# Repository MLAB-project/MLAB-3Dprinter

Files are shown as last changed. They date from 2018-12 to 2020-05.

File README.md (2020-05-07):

RebeliX
=======
RebeliX – a 3D printer inspired by constructions of Rebel II a Prusa i3. Licensed as GPLv3. Howto and list of materials is available on www.RebeliX.cz (currently only in Czech, we are working on it, help is appreciated).

Features
=====

* Piezoelectric based precise Z-calibration
* Symmetric motor configuration push-pull to minimize belt stretching in printing of corners

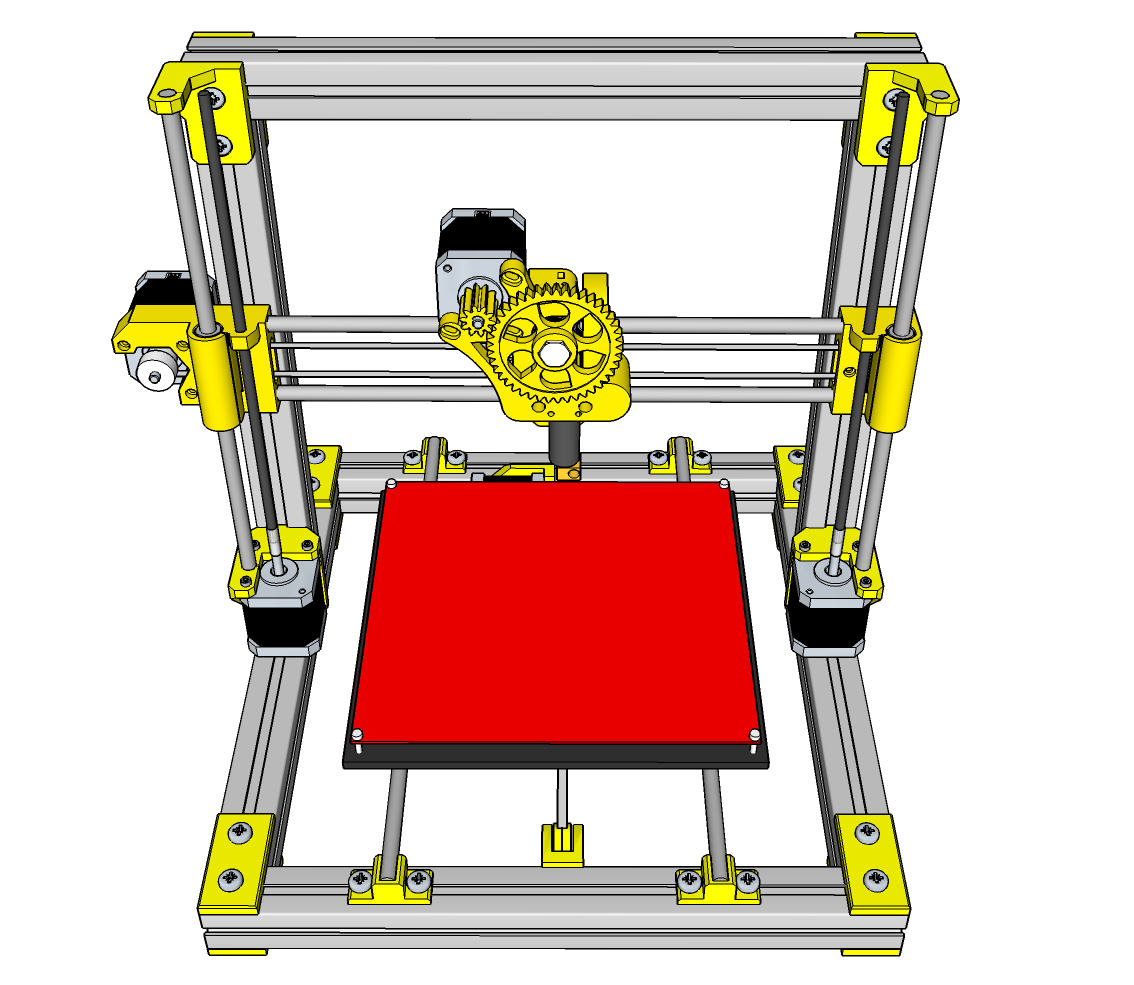
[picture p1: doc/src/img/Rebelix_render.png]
RebeliX Preview of assembled printer


Build
=====

   sudo pip install stlsort

To continue OpenSCAD has to be installed and available as `openscad` command.

1. Make necessary changes to configuration.scad according to printer that prints the parts and available hardware. 
* Generate a calibration object by `make calibration`.
* Print generated calibration.stl and repeat the steps if unhappy.

When satisfied, run `make clean && make all`. That produces STLs with your tweeks.

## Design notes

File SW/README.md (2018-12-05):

Configuration for Rebelix after editing for MLAB

Configuration.h used to generate printer firmware by configurator available from there:
https://www.repetier.com/firmware/v092/index.php

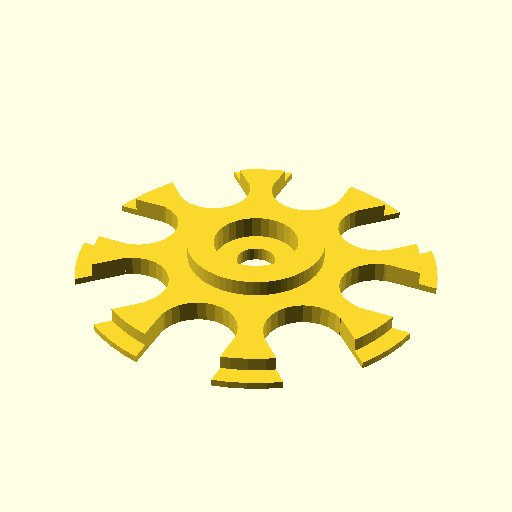
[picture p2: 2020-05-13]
doc/src/img/spool-center.png

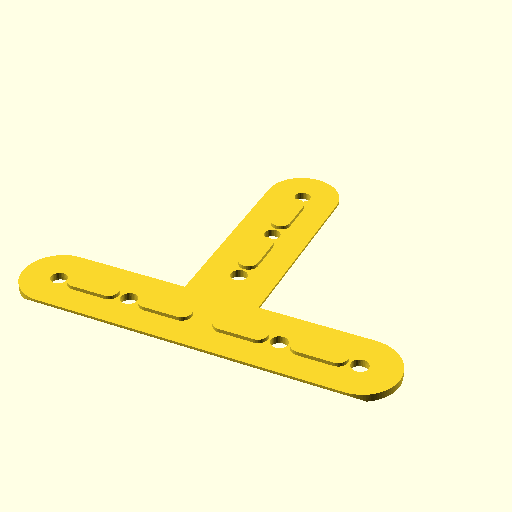
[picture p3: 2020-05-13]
doc/src/img/z-coupler.png

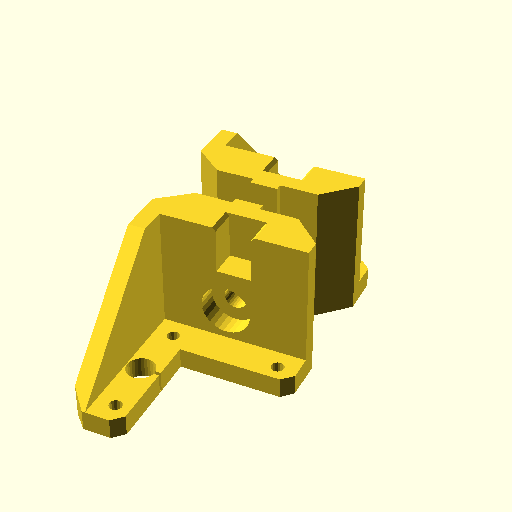
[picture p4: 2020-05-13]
doc/src/img/z-bottom.png

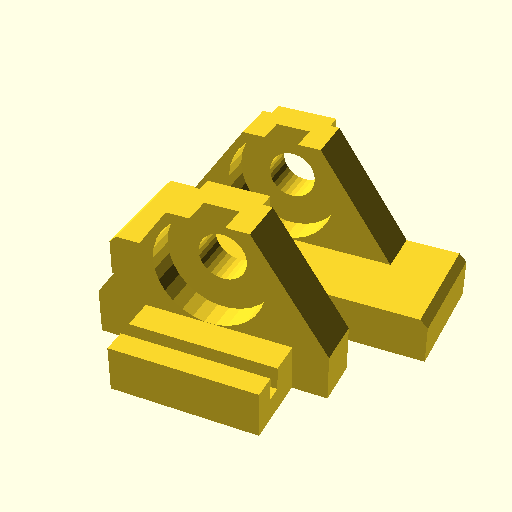
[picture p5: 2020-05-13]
doc/src/img/RAMPS_mini.png

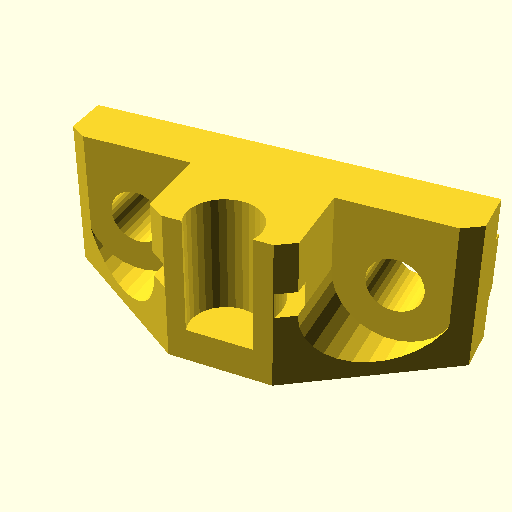
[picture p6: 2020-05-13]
doc/src/img/y-rod-holder.png

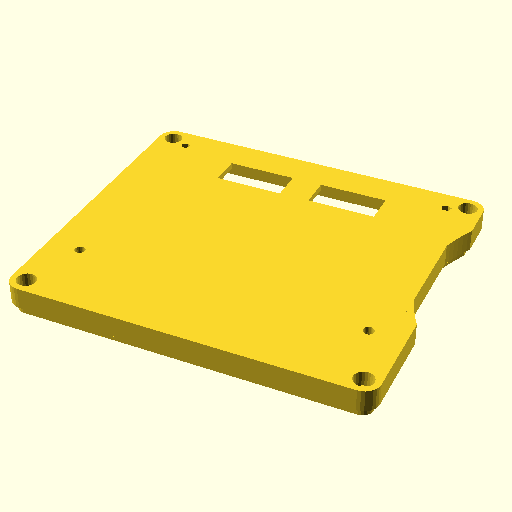
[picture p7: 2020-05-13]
doc/src/img/mods_for_display_case_back.png

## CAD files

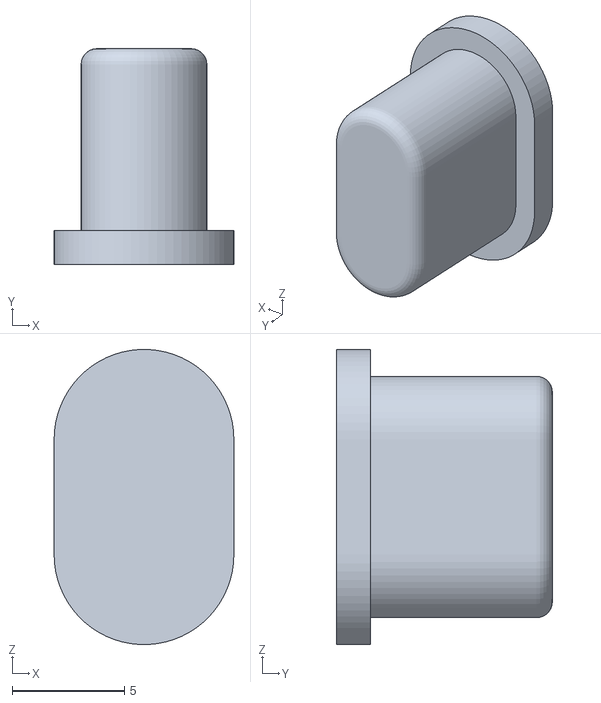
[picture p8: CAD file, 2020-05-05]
hw/cad/src/include/Case_for_the_Full_Graphic_Smart_LCD_Controllerf-Kill_Button_FGD.stl
8.00 x 9.60 x 13.1

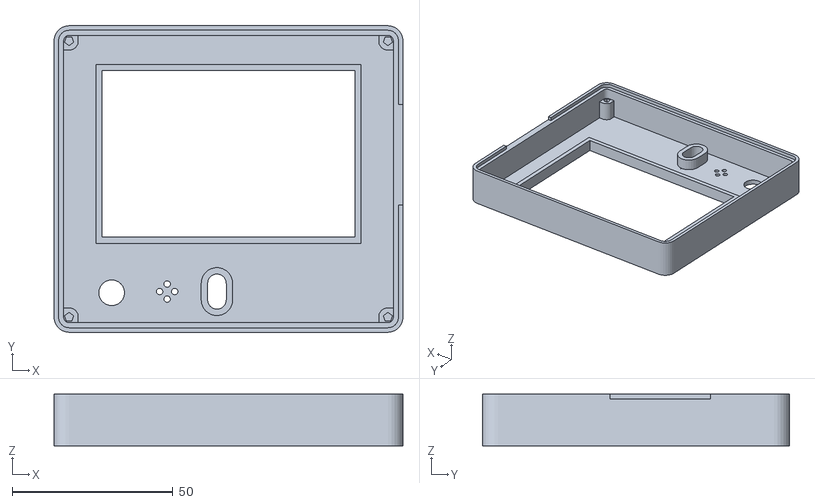
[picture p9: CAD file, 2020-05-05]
hw/cad/src/include/Case_for_the_Full_Graphic_Smart_LCD-Top_Case_FGD.stl
108.6 x 95.4 x 16.1

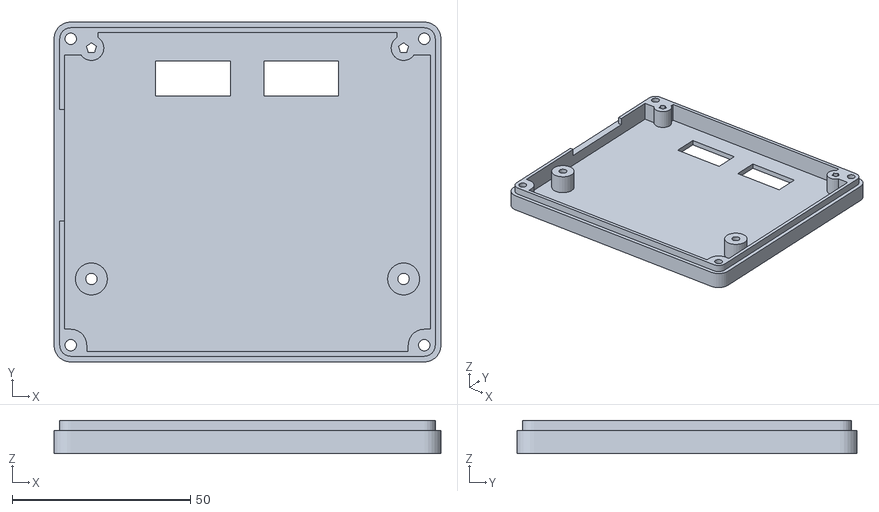
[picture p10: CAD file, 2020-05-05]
hw/cad/src/include/Case_for_the_Full_Graphic_Smart_LCD_Controller-Bottom_Case_FGD.stl
108.6 x 95.4 x 9.30

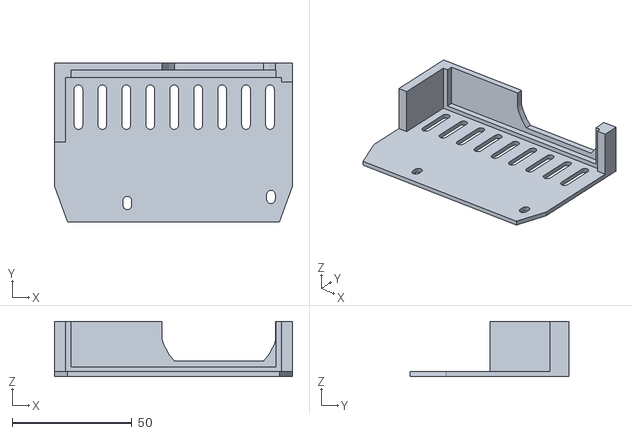
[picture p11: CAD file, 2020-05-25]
doc/src/stl/Rear_EURO_12V_240W.stl
99.4 x 66.5 x 23.0

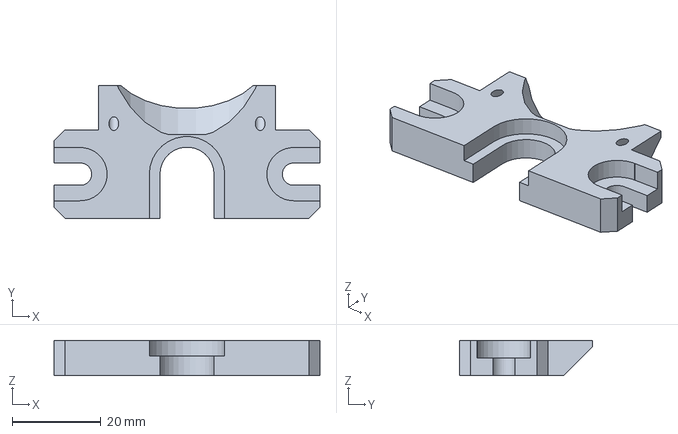
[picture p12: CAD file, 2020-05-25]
hw/amf/j-head-mount.amf
60.0 x 30.0 x 8.00 mm

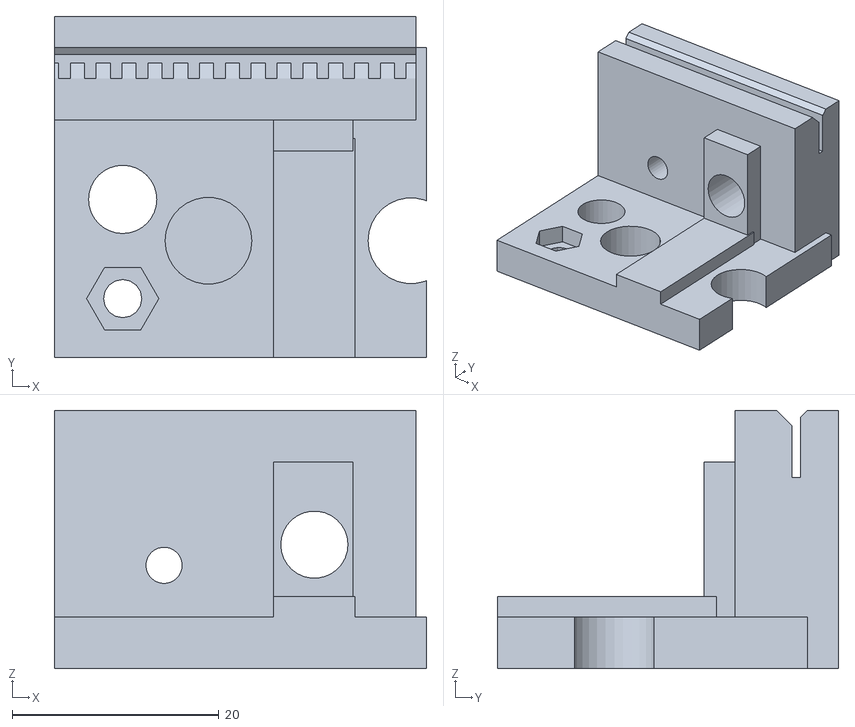
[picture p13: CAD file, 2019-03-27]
hw/cad/calibration.stl
36.0 x 33.0 x 25.0

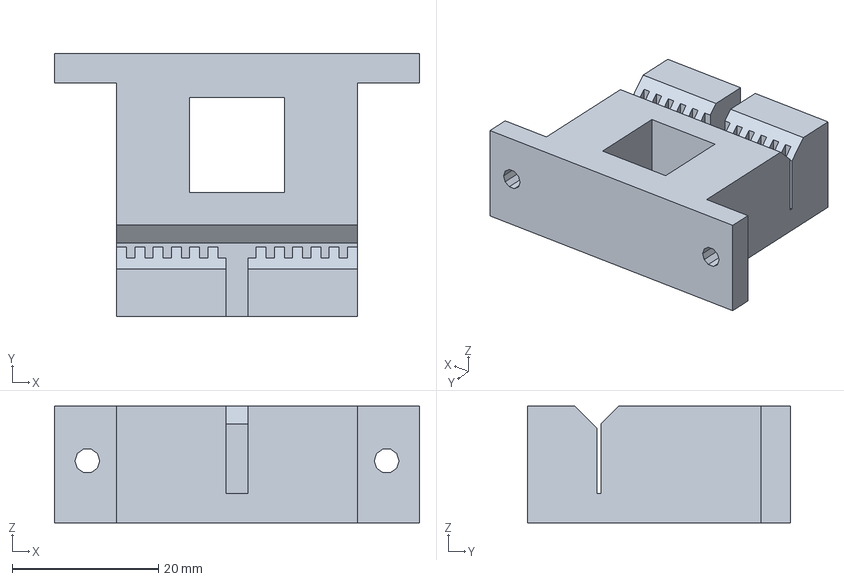
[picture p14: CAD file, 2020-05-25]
hw/amf/y-belt-holder.amf
50.0 x 36.0 x 16.0 mm

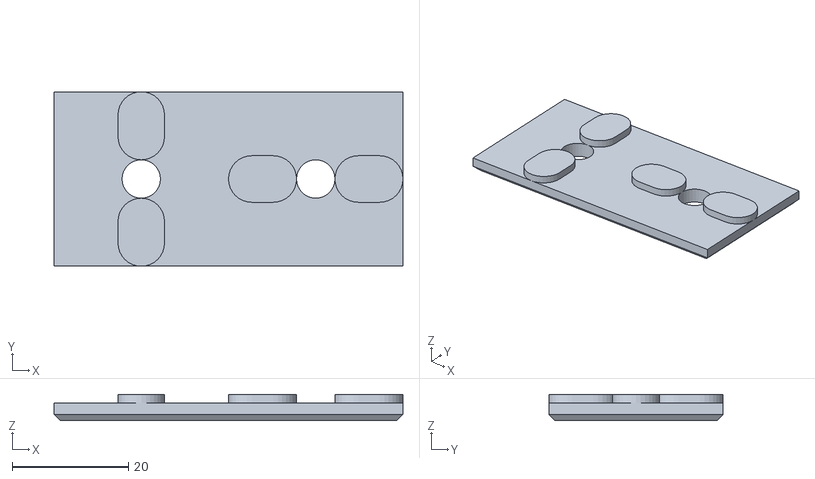
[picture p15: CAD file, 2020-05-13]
doc/src/stl/corner-coupler.stl
60.0 x 30.0 x 4.50

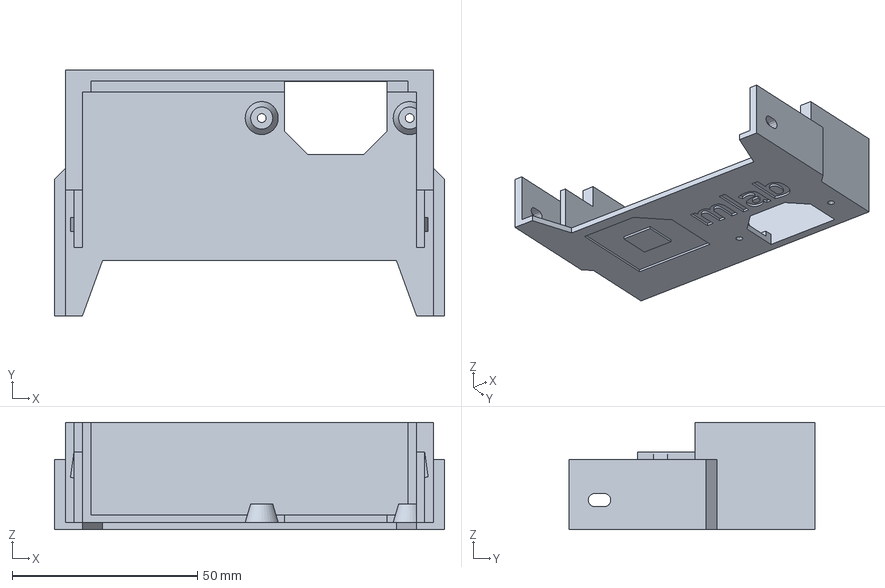
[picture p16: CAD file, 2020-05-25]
hw/amf/Front_EURO_12V_240W.amf
105.4 x 66.5 x 29.0 mm

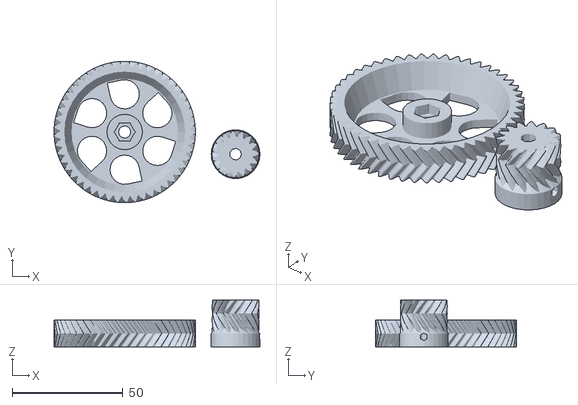
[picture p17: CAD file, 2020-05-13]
doc/src/stl/wade-gears.stl
92.9 x 63.7 x 21.0

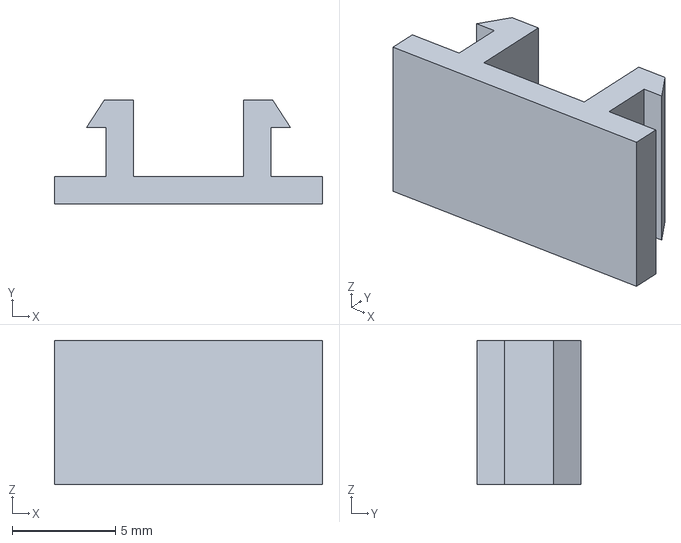
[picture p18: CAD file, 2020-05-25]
hw/amf/cable-holder.amf
13.0 x 5.04 x 7.00 mm

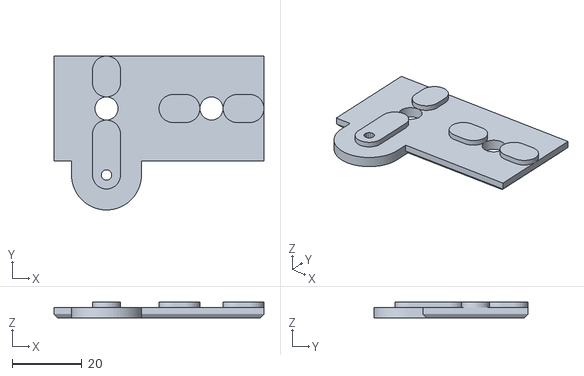
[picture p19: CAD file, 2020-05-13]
doc/src/stl/corner-coupler-bottom.stl
60.0 x 44.0 x 4.50

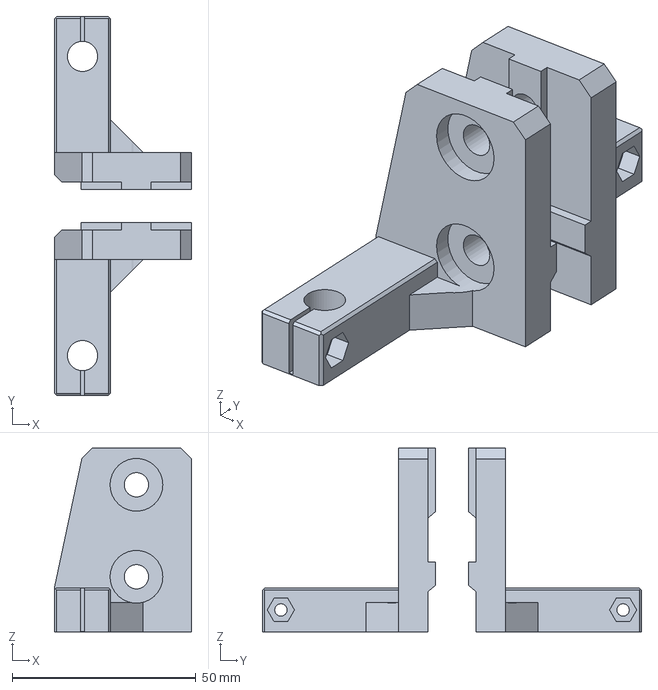
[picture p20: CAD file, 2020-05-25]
hw/amf/z-top.amf
37.3 x 103.0 x 50.0 mm

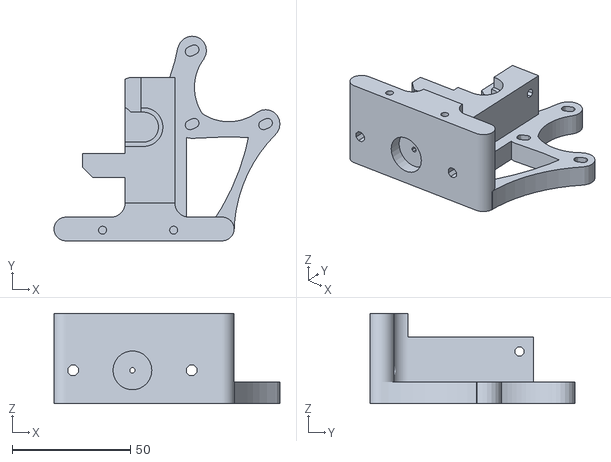
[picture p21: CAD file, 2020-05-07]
doc/src/stl/gregs-wade-625.stl
95.4 x 86.4 x 38.0

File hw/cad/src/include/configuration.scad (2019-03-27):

// Layer high for the printing [mm]
layer_height = 0.20; //Slic3r->Print Settings->Layers and perimeters->Layer height

// Spare for the screws heads [mm]
spare = 0.75;
// M6 screw diameter [mm]
M6_head_diameter = 13.6+spare;
//M6_head_diameter = 10.6+spare;
//M6_head_diameter = 12+spare;

// M6 head high (for hiding it) [mm]
//M6_head_height = 4;
M6_head_height = 3.6;
//M6_head_height = 4.5;

// Screws and rods diameters
M8_smooth_rod_diameter = 8.3;
M8_smooth_rod_diameter_catch = 8.4;
// Prumer 8mm tyce
rod_8mm_d = 8.2; //pro dil z-top
M6_diameter = 6.6;
M6_dia=M6_diameter; //pro dil z-top
M6_diamater_horizontal = 6.5;
M3_diameter = 3.7;
M3_diameter_horizontal = 3.5;

//matice trapézové tyče
TRAP_diameter_externa=22; //průmer vnější 


// Nuts diameters
M3_nut_diameter = 7.0;
M3_nut_diameter_horizontal = 6.7;

// ALU profile parameters
ALU_cut_width = 7.9;
ALU_cut_width_horizontal = 7.7;

// Sirka matky do profilu (pokud neni pouzita, tak 0)
//profile_nut_width = 9.5;
profile_nut_width = 0; //pro z-top

// Motors length/depth (for axes Z and Y)
//SX17-1003LQFE (recommended for the Z axis)
motor_length = 29.5;
//SX17-1003 (recommended for the Z axis)
//motor_length = 34;
//SX17-1005
//motor_length = 40;
//SX17-0905 - this motor is too high - the Z end stop holder has to be adjusted
//motor_length = 48;

// Extrusion width [mm]
extrusion_width = 0.66; //Slic3r->Print Settings->Advanced->Default extrusion width

/// Belt type ******************************************************

// GT2 
/*belt_tooth_distance = 2;
belt_tooth_ratio = 0.5;
belt_tooth_height = 1.4;
belt_thickness = 2.3;
*/

// T2.5
belt_tooth_distance = 2.5;
belt_tooth_ratio = 0.45;


// Tloustka rohovych spojek
// 5 mm => sroub M6x14 s podlozkou
// 3 mm => sroub M6x12 s podlozkou
coupler_thickness = 3;

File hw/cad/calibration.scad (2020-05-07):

include <./src/include/configuration.scad>

difference(){
	union(){
		cube([36,30,5]);
		translate([0,23,0])cube([35,10,25]);
		translate([M6_diameter*2+8,20,0])cube([ALU_cut_width_horizontal,11,20]);
	}
	translate([M6_diameter,M6_diameter+M3_diameter+5,-1])cylinder(r=M6_diameter/2,h=7,$fn=32);
	translate([M6_diameter,M3_diameter+2,-1]){
		cylinder(r=M3_diameter/2,h=7,$fn=16);	
		translate([0,0,3.5])cylinder(r=M3_nut_diameter/2,h=2.6,$fn=6);
	}
	translate([M6_diameter+M8_smooth_rod_diameter,M8_smooth_rod_diameter+3,layer_height])cylinder(h=7,r=M8_smooth_rod_diameter_catch/2,$fn = 30);
	translate([34.5,M8_smooth_rod_diameter+3,-1])cylinder(h=7,r=M8_smooth_rod_diameter/2,$fn = 30);
	
	translate([M6_diameter+4,34,10]) 
	rotate([90,0,0]){
		cylinder(h = 15, r=M3_diameter_horizontal/2, $fn=30);
		cylinder(h = 4, r=M3_nut_diameter_horizontal/2, $fn=6);
	}

	translate([M6_diameter*2+8+ALU_cut_width/2,34,12]) 
	rotate([90,0,0]){
		cylinder(r = M6_diamater_horizontal/2, h = 15, $fn = 30);
		cylinder(r = M6_head_diameter/2, h = 4, $fn = 30);
	}
	
	translate([-1,27,18.5])belt_holder_beltcut();
}

translate([M6_diameter*2+8,0,0])cube([ALU_cut_width,M6_diameter*2+8,7]);

module belt_holder_beltcut(){
 echo(belt_tooth_ratio*belt_tooth_distance);
 position_tweak=-1.1;
 // Belt slit
 //translate([-66,-0.5+10,3]) 
 translate([0,1.5,0])
 cube([67,0.8,15]);
 // Smooth insert cutout
 //translate([-66,-0.5+10,12]) 
 translate([0,1.5,5])
 rotate([45,0,0]) cube([67,15,15]);
 // Individual teeth
 for ( i = [0 : 23] ){
 	translate([0+i*belt_tooth_distance+position_tweak,0,0]) cube([belt_tooth_ratio*belt_tooth_distance,1.7,15]);
 }
}

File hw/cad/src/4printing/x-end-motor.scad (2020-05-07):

// PRUSA iteration3
// x end motor
// GNU GPL v3
// Josef Průša <iam@josefprusa.cz> and contributors
// http://www.reprap.org/wiki/Prusa_Mendel
// http://prusamendel.org

use <../include/x-end.scad>
include <../include/configuration.scad>

module x_end_motor_base(){
 x_end_base();
 translate(v=[-15,31,26.5]) cube(size = [17,44,53], center = true);
}

module x_end_motor_holes(){
 x_end_holes();
 // Position to place
 translate(v=[-1,32,30.25]){
  // Belt hole
  translate(v=[-14,1,0]) cube(size = [10,46,22], center = true);
  // Motor mounting holes
  //translate(v=[20,-15.5,-15.5]) rotate(a=[0,-90,0]) rotate(a=[0,0,90]) cylinder(h = 70, r=1.8, $fn=30);
  //translate(v=[1,-15.5,-15.5]) rotate(a=[0,-90,0]) rotate(a=[0,0,90]) cylinder(h = 10, r=3.1, $fn=30);
  
  hull(){
    translate(v=[20,-16.5,-15.5]) rotate(a=[0,-90,0]) rotate(a=[0,0,90]) cylinder(h = 70, r=M3_diameter_horizontal/2, $fn=30);
    translate(v=[20,-14.5,-15.5]) rotate(a=[0,-90,0]) rotate(a=[0,0,90]) cylinder(h = 70, r=M3_diameter_horizontal/2, $fn=30);
  }
  hull(){
    translate(v=[1,-16.5,-15.5]) rotate(a=[0,-90,0]) rotate(a=[0,0,90]) cylinder(h = 10, r=3.1, $fn=30);
    translate(v=[1,-14.5,-15.5]) rotate(a=[0,-90,0]) rotate(a=[0,0,90]) cylinder(h = 10, r=3.1, $fn=30);
  }

  hull(){
    translate(v=[20,-16.5,15.5]) rotate(a=[0,-90,0]) rotate(a=[0,0,90]) cylinder(h = 70, r=M3_diameter_horizontal/2, $fn=30);
    translate(v=[20,-14.5,15.5]) rotate(a=[0,-90,0]) rotate(a=[0,0,90]) cylinder(h = 70, r=M3_diameter_horizontal/2, $fn=30);
  }
  hull(){
    translate(v=[1,-16.5,15.5]) rotate(a=[0,-90,0]) rotate(a=[0,0,90]) cylinder(h = 10, r=3.1, $fn=30);
    translate(v=[1,-14.5,15.5]) rotate(a=[0,-90,0]) rotate(a=[0,0,90]) cylinder(h = 10, r=3.1, $fn=30);
  }

  hull(){
    translate(v=[20,16.5,-15.5]) rotate(a=[0,-90,0]) rotate(a=[0,0,90]) cylinder(h = 70, r=M3_diameter_horizontal/2, $fn=30);
    translate(v=[20,14.5,-15.5]) rotate(a=[0,-90,0]) rotate(a=[0,0,90]) cylinder(h = 70, r=M3_diameter_horizontal/2, $fn=30);
  }
  hull(){
    translate(v=[1,16.5,-15.5]) rotate(a=[0,-90,0]) rotate(a=[0,0,90]) cylinder(h = 10, r=3.1, $fn=30);
    translate(v=[1,14.5,-15.5]) rotate(a=[0,-90,0]) rotate(a=[0,0,90]) cylinder(h = 10, r=3.1, $fn=30);
  }
 
  // Material saving cutout 
  translate(v=[-10,12,10]) cube(size = [60,42,42], center = true);

  // Material saving cutout
  translate(v=[-10,40,-30]) rotate(a=[45,0,0])  cube(size = [60,42,42], center = true);
  // Motor shaft cutout
  translate(v=[0,0,0]) rotate(a=[0,-90,0]) rotate(a=[0,0,90]) cylinder(h = 70, r=17, $fn=6);
 }
}

// Final part
module x_end_motor(){
 difference(){
  x_end_motor_base();
  x_end_motor_holes();
 }

 translate([30,0,0]) mirror([1,0,0])
   difference(){
    x_end_motor_base();
    x_end_motor_holes();
   }
}

x_end_motor();

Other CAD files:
hw/cad/src/include/x-carriage.stl
doc/src/stl/mods_for_display_case_front.stl
hw/amf/gregs-wade-625.amf
doc/src/stl/extruder_fan.stl
hw/cad/src/4printing/y-motor.scad
doc/src/stl/Front_EURO_12V_240W.stl
doc/src/stl/RAMPS_mini.stl
doc/src/stl/cable-holder-Nema17.stl
doc/src/stl/cable-holder.stl
doc/src/stl/extruder-idler.stl
doc/src/stl/extruder-washer.stl
doc/src/stl/filament_cleaner.stl
doc/src/stl/heatbed-nut.stl
doc/src/stl/j-head-mount.stl
doc/src/stl/mods_for_display_case_back.stl
doc/src/stl/mods_for_display_case_button.stl
doc/src/stl/profile-cover-hole.stl
doc/src/stl/profile-cover.stl
doc/src/stl/spool-center.stl
doc/src/stl/spool-holder.stl
doc/src/stl/spool_bearing.stl
doc/src/stl/x-carriage.stl
doc/src/stl/x-end-motor.stl
doc/src/stl/y-LM8UU-holder.stl
doc/src/stl/y-belt-holder.stl
doc/src/stl/y-motor.stl
doc/src/stl/y-rod-holder.stl
doc/src/stl/z-bottom.stl
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

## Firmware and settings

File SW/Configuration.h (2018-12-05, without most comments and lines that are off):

#define CONFIGURATION_H
#define NUM_EXTRUDER 1
#define MOTHERBOARD 33
#include "pins.h"
#undef FAN_PIN
#define FAN_PIN 9
#undef FAN_BOARD_PIN
#define FAN_BOARD_PIN -1
#define BOARD_FAN_SPEED 255
#define FAN_THERMO_PIN -1
#define FAN_THERMO_MIN_PWM 128
#define FAN_THERMO_MAX_PWM 255
#define FAN_THERMO_MIN_TEMP 45
#define FAN_THERMO_MAX_TEMP 60
#define FAN_THERMO_THERMISTOR_PIN -1
#define FAN_THERMO_THERMISTOR_TYPE 1
#define BLUETOOTH_SERIAL  -1
#define BLUETOOTH_BAUD  115200
#define MIXING_EXTRUDER 0
#define DRIVE_SYSTEM 0
#define XAXIS_STEPS_PER_MM 80
#define YAXIS_STEPS_PER_MM 80
#define ZAXIS_STEPS_PER_MM 408.15
#define EXTRUDER_FAN_COOL_TEMP 50
#define PDM_FOR_EXTRUDER 0
#define PDM_FOR_COOLER 0
#define DECOUPLING_TEST_MAX_HOLD_VARIANCE 20
#define DECOUPLING_TEST_MIN_TEMP_RISE 1
#define KILL_IF_SENSOR_DEFECT 0
#define RETRACT_ON_PAUSE 2
#define PAUSE_START_COMMANDS ""
#define PAUSE_END_COMMANDS ""
#define SHARED_EXTRUDER_HEATER 0
#define EXT0_X_OFFSET 0
#define EXT0_Y_OFFSET 0
#define EXT0_Z_OFFSET 0
#define EXT0_STEPS_PER_MM 514
#define EXT0_TEMPSENSOR_TYPE 14
#define EXT0_TEMPSENSOR_PIN TEMP_0_PIN
#define EXT0_HEATER_PIN HEATER_0_PIN
#define EXT0_STEP_PIN ORIG_E0_STEP_PIN
#define EXT0_DIR_PIN ORIG_E0_DIR_PIN
#define EXT0_INVERSE 1
#define EXT0_ENABLE_PIN ORIG_E0_ENABLE_PIN
#define EXT0_ENABLE_ON 0
#define EXT0_MIRROR_STEPPER 0
#define EXT0_STEP2_PIN ORIG_E0_STEP_PIN
#define EXT0_DIR2_PIN ORIG_E0_DIR_PIN
#define EXT0_INVERSE2 0
#define EXT0_ENABLE2_PIN ORIG_E0_ENABLE_PIN
#define EXT0_MAX_FEEDRATE 50
#define EXT0_MAX_START_FEEDRATE 20
#define EXT0_MAX_ACCELERATION 1000
#define EXT0_HEAT_MANAGER 3
#define EXT0_WATCHPERIOD 1
#define EXT0_PID_INTEGRAL_DRIVE_MAX 250
#define EXT0_PID_INTEGRAL_DRIVE_MIN 100
#define EXT0_PID_PGAIN_OR_DEAD_TIME 2
#define EXT0_PID_I 6
#define EXT0_PID_D 40
#define EXT0_PID_MAX 255
#define EXT0_ADVANCE_K 0
#define EXT0_ADVANCE_L 0
#define EXT0_ADVANCE_BACKLASH_STEPS 0
#define EXT0_WAIT_RETRACT_TEMP 150
#define EXT0_WAIT_RETRACT_UNITS 0
#define EXT0_SELECT_COMMANDS ""
#define EXT0_DESELECT_COMMANDS ""
#define EXT0_EXTRUDER_COOLER_PIN 8
#define EXT0_EXTRUDER_COOLER_SPEED 255
#define EXT0_DECOUPLE_TEST_PERIOD 12000
#define EXT0_JAM_PIN -1
#define EXT0_JAM_PULLUP 0
#define FEATURE_RETRACTION 1
#define AUTORETRACT_ENABLED 0
#define RETRACTION_LENGTH 3
#define RETRACTION_LONG_LENGTH 13
#define RETRACTION_SPEED 40
#define RETRACTION_Z_LIFT 0
#define RETRACTION_UNDO_EXTRA_LENGTH 0
#define RETRACTION_UNDO_EXTRA_LONG_LENGTH 0
#define RETRACTION_UNDO_SPEED 20
#define FILAMENTCHANGE_X_POS 0
#define FILAMENTCHANGE_Y_POS 0
#define FILAMENTCHANGE_Z_ADD  2
#define FILAMENTCHANGE_REHOME 1
#define FILAMENTCHANGE_SHORTRETRACT 5
#define FILAMENTCHANGE_LONGRETRACT 50
#define JAM_STEPS 220
#define JAM_SLOWDOWN_STEPS 320
#define JAM_SLOWDOWN_TO 70
#define JAM_ERROR_STEPS 500
#define JAM_MIN_STEPS 10
#define JAM_ACTION 1
#define RETRACT_DURING_HEATUP true
#define PID_CONTROL_RANGE 10
#define SKIP_M109_IF_WITHIN 2
#define SCALE_PID_TO_MAX 0
#define TEMP_HYSTERESIS 0
#define EXTRUDE_MAXLENGTH 160
#define NUM_TEMPS_USERTHERMISTOR0 0
#define USER_THERMISTORTABLE0 {}
#define NUM_TEMPS_USERTHERMISTOR1 0
#define USER_THERMISTORTABLE1 {}
#define NUM_TEMPS_USERTHERMISTOR2 0
#define USER_THERMISTORTABLE2 {}
#define GENERIC_THERM_VREF 5
#define GENERIC_THERM_NUM_ENTRIES 33
#define HEATER_PWM_SPEED 0
#define HAVE_HEATED_BED 0
#define HEATED_BED_MAX_TEMP 120
#define SKIP_M190_IF_WITHIN 3
#define HEATED_BED_SENSOR_TYPE 14
#define HEATED_BED_SENSOR_PIN TEMP_1_PIN
#define HEATED_BED_HEATER_PIN HEATER_1_PIN
#define HEATED_BED_SET_INTERVAL 5000
#define HEATED_BED_HEAT_MANAGER 3
#define HEATED_BED_PID_INTEGRAL_DRIVE_MAX 255
#define HEATED_BED_PID_INTEGRAL_DRIVE_MIN 80
#define HEATED_BED_PID_PGAIN_OR_DEAD_TIME   2
#define HEATED_BED_PID_IGAIN   18.38
#define HEATED_BED_PID_DGAIN 530.16
#define HEATED_BED_PID_MAX 255
#define HEATED_BED_DECOUPLE_TEST_PERIOD 300000
#define MIN_EXTRUDER_TEMP 150
#define MAXTEMP 248
#define MIN_DEFECT_TEMPERATURE -30
#define MAX_DEFECT_TEMPERATURE 255
#define SUPPORT_LASER 0
#define LASER_PIN -1
#define LASER_ON_HIGH 1
#define SUPPORT_CNC 0
#define CNC_WAIT_ON_ENABLE 300
#define CNC_WAIT_ON_DISABLE 0
#define CNC_ENABLE_PIN -1
#define CNC_ENABLE_WITH 1
#define CNC_DIRECTION_PIN -1
#define CNC_DIRECTION_CW 1
#define DEFAULT_PRINTER_MODE 0
#define ENDSTOP_PULLUP_X_MIN true
#define ENDSTOP_X_MIN_INVERTING false
#define MIN_HARDWARE_ENDSTOP_X true
#define ENDSTOP_PULLUP_Y_MIN true
#define ENDSTOP_Y_MIN_INVERTING false
#define MIN_HARDWARE_ENDSTOP_Y true
#define ENDSTOP_PULLUP_Z_MIN false
#define ENDSTOP_Z_MIN_INVERTING true
#define MIN_HARDWARE_ENDSTOP_Z true
#define ENDSTOP_PULLUP_X_MAX true
#define ENDSTOP_X_MAX_INVERTING false
#define MAX_HARDWARE_ENDSTOP_X false
#define ENDSTOP_PULLUP_Y_MAX true
#define ENDSTOP_Y_MAX_INVERTING false
#define MAX_HARDWARE_ENDSTOP_Y false
#define ENDSTOP_PULLUP_Z_MAX true
#define ENDSTOP_Z_MAX_INVERTING false
#define MAX_HARDWARE_ENDSTOP_Z false
#define max_software_endstop_r true
#define min_software_endstop_x false
#define min_software_endstop_y false
#define min_software_endstop_z false
#define max_software_endstop_x true
#define max_software_endstop_y true
#define max_software_endstop_z true
#define ENDSTOP_X_BACK_MOVE 5
#define ENDSTOP_Y_BACK_MOVE 5
#define ENDSTOP_Z_BACK_MOVE 10
#define ENDSTOP_X_RETEST_REDUCTION_FACTOR 2
#define ENDSTOP_Y_RETEST_REDUCTION_FACTOR 2
#define ENDSTOP_Z_RETEST_REDUCTION_FACTOR 0
#define ENDSTOP_X_BACK_ON_HOME 1
#define ENDSTOP_Y_BACK_ON_HOME 1
#define ENDSTOP_Z_BACK_ON_HOME 0
#define ALWAYS_CHECK_ENDSTOPS 0
#define X_ENABLE_ON 0
#define Y_ENABLE_ON 0
#define Z_ENABLE_ON 0
#define DISABLE_X 0
#define DISABLE_Y 0
#define DISABLE_Z 1
#define DISABLE_E 0
#define INVERT_X_DIR 0
#define INVERT_Y_DIR 1
#define INVERT_Z_DIR 0
#define X_HOME_DIR -1
#define Y_HOME_DIR -1
#define Z_HOME_DIR -1
#define X_MAX_LENGTH 185
#define Y_MAX_LENGTH 180
#define Z_MAX_LENGTH 185
#define X_MIN_POS 0
#define Y_MIN_POS 0
#define Z_MIN_POS 0
#define DISTORTION_CORRECTION 1
#define DISTORTION_CORRECTION_POINTS 5
#define DISTORTION_CORRECTION_R 100
#define DISTORTION_PERMANENT 1
#define DISTORTION_UPDATE_FREQUENCY 15
#define DISTORTION_START_DEGRADE 0.5
#define DISTORTION_END_HEIGHT 1
#define DISTORTION_EXTRAPOLATE_CORNERS 0
#define DISTORTION_XMIN 10
#define DISTORTION_YMIN 10
#define DISTORTION_XMAX 190
#define DISTORTION_YMAX 190
#define FEATURE_BABYSTEPPING 1
#define BABYSTEP_MULTIPLICATOR 80
#define DELTA_SEGMENTS_PER_SECOND_PRINT 180 // Move accurate setting for print moves
#define DELTA_SEGMENTS_PER_SECOND_MOVE 70 // Less accurate setting for other moves
#define EXACT_DELTA_MOVES 1
#define DELTA_HOME_ON_POWER 0
#define DELTASEGMENTS_PER_PRINTLINE 24
#define STEPPER_INACTIVE_TIME 360L
#define MAX_INACTIVE_TIME 0L
#define MAX_FEEDRATE_X 80
#define MAX_FEEDRATE_Y 80
#define MAX_FEEDRATE_Z 30
#define HOMING_FEEDRATE_X 50
#define HOMING_FEEDRATE_Y 50
#define HOMING_FEEDRATE_Z 15
#define HOMING_ORDER HOME_ORDER_XYZ
#define ZHOME_MIN_TEMPERATURE 0
#define ZHOME_HEAT_ALL 1
#define ZHOME_HEAT_HEIGHT 20
#define ZHOME_X_POS 999999
#define ZHOME_Y_POS 999999
#define ENABLE_BACKLASH_COMPENSATION 0
#define X_BACKLASH 0
#define Y_BACKLASH 0
#define Z_BACKLASH 0
#define RAMP_ACCELERATION 1
#define STEPPER_HIGH_DELAY 1
#define DIRECTION_DELAY 0
#define STEP_DOUBLER_FREQUENCY 12000
#define ALLOW_QUADSTEPPING 1
#define DOUBLE_STEP_DELAY 1 // time in microseconds
#define MAX_ACCELERATION_UNITS_PER_SQ_SECOND_X 1000
#define MAX_ACCELERATION_UNITS_PER_SQ_SECOND_Y 1000
#define MAX_ACCELERATION_UNITS_PER_SQ_SECOND_Z 500
#define MAX_TRAVEL_ACCELERATION_UNITS_PER_SQ_SECOND_X 1000
#define MAX_TRAVEL_ACCELERATION_UNITS_PER_SQ_SECOND_Y 1000
#define MAX_TRAVEL_ACCELERATION_UNITS_PER_SQ_SECOND_Z 500
#define INTERPOLATE_ACCELERATION_WITH_Z 0
#define ACCELERATION_FACTOR_TOP 100
#define MAX_JERK 30
#define MAX_ZJERK 0.3
#define PRINTLINE_CACHE_SIZE 16
#define MOVE_CACHE_LOW 10
#define LOW_TICKS_PER_MOVE 250000
#define EXTRUDER_SWITCH_XY_SPEED 100
#define DUAL_X_AXIS 0
#define FEATURE_TWO_XSTEPPER 0
#define X2_STEP_PIN   ORIG_E1_STEP_PIN
#define X2_DIR_PIN    ORIG_E1_DIR_PIN
#define X2_ENABLE_PIN ORIG_E1_ENABLE_PIN
#define FEATURE_TWO_YSTEPPER 0
#define Y2_STEP_PIN   ORIG_E1_STEP_PIN
#define Y2_DIR_PIN    ORIG_E1_DIR_PIN
#define Y2_ENABLE_PIN ORIG_E1_ENABLE_PIN
#define FEATURE_TWO_ZSTEPPER 0
#define Z2_STEP_PIN   ORIG_E1_STEP_PIN
#define Z2_DIR_PIN    ORIG_E1_DIR_PIN
#define Z2_ENABLE_PIN ORIG_E1_ENABLE_PIN
#define FEATURE_THREE_ZSTEPPER 0
#define Z3_STEP_PIN   ORIG_E2_STEP_PIN
#define Z3_DIR_PIN    ORIG_E2_DIR_PIN
#define Z3_ENABLE_PIN ORIG_E2_ENABLE_PIN
#define FEATURE_DITTO_PRINTING 0
#define USE_ADVANCE 0
#define ENABLE_QUADRATIC_ADVANCE 0
#define BAUDRATE 115200
#define ENABLE_POWER_ON_STARTUP 0
#define POWER_INVERTING 0
#define KILL_METHOD 1
#define ACK_WITH_LINENUMBER 1
#define WAITING_IDENTIFIER "wait"
#define ECHO_ON_EXECUTE 1
#define EEPROM_MODE 1
#undef PS_ON_PIN
#define PS_ON_PIN -1
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

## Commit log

2018-12-05 Always check endstops disabled. FIX #8
    [Configuration.h]
2019-03-26 Switch to GT2.5 belts and render calibration model.
    [calibration.stl, configuration.scad]
2019-03-27 Increase tooth thickness.
    [calibration.stl, configuration.scad]
2019-03-27 Tightening belt holder.
    [calibration.stl]
2019-03-27 Parameter change related to rendered model.
    [configuration.scad]
2020-04-30 bigger heat-bead levelling wheel
    [heatbed-nut.scad, heatbed-nut.stl]
2020-05-05 Revert accidental delete of source STL files.
    [Case_for_the_Full_Graphic_Smart_LCD-Top_Case_FGD.stl, Case_for_the_Full_Graphic_Smart_LCD_Controller-Bottom_Case_FGD.stl, mods_for_display_case_back.stl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]
2020-05-05 Add mising STL source file.
    [Case_for_the_Full_Graphic_Smart_LCD_Controllerf-Kill_Button_FGD.stl, mods_for_display_case.scad]
2020-05-05 Fixed logo depth #24
    [mods_for_display_case.scad]
2020-05-06 fix WARNING: Too many unnamed arguments supplied, in file gregs-wade-625.scad, line 399
    [gregs-wade-625.scad]
2020-05-07 UniversalScientificTechnologies/MLAB-3Dprinter#28 Moved preview STL files to doc/src/stl and included STL files hw/cad/src/include folder.
    [Case_for_the_Full_Graphic_Smart_LCD-Top_Case_FGD.stl, Case_for_the_Full_Graphic_Smart_LCD_Controller-Bottom_Case_FGD.stl, Case_for_the_Full_Graphic_Smart_LCD_C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]
2020-05-07 UniversalScientificTechnologies/MLAB-3Dprinter#28 Moved AMF files to hw/amf folder.
    [cable-holder.amf, corner-coupler.amf, extruder-idler.amf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]
2020-05-07 UniversalScientificTechnologies/MLAB-3Dprinter#28 Moved Makefile and related files to hw/cad/src, included files to hw/cad/src/include and print files to hw/cad/src/4printing folders.
    [Front_EURO_12V_240W.scad, MLAB_logo.scad, RAMPS_mini.scad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]
2020-05-07 UniversalScientificTechnologies/MLAB-3Dprinter#28 Updated Makefile and related SCAD files.
    [Front_EURO_12V_240W.scad, RAMPS_mini.scad, Rear_EURO_12V_240W.scad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]
2020-05-07 UniversalScientificTechnologies/MLAB-3Dprinter#28 Removed Extruder_filament_3mm.
    [bearing-guide.scad, conf_bushing.scad, extruder-idler.scad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]
2020-05-07 UniversalScientificTechnologies/MLAB-3Dprinter#28 Removed unused sources and includes.
    [RAMPS_mini.scad, SlidingBoxV13.scad, bearing-guide.scad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]
2020-05-07 UniversalScientificTechnologies/MLAB-3Dprinter#28 Fixed include/use/import paths in source files
    [Front_EURO_12V_240W.scad, Rear_EURO_12V_240W.scad, calibration.scad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]
2020-05-07 UniversalScientificTechnologies/MLAB-3Dprinter#28 Added missing dependency x-carriage.stl as symbolic link from doc/src/stl
    [x-carriage.stl]
2020-05-07 UniversalScientificTechnologies/MLAB-3Dprinter#28 Added missing AMF files
    [Front_EURO_12V_240W.amf, RAMPS_mini.amf, Rear_EURO_12V_240W.amf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]
2020-05-07 UniversalScientificTechnologies/MLAB-3Dprinter#28 Removed unused AMF files
    [wade-gears_big.amf, x-end-idler.amf, y-idler.amf]
2020-05-07 UniversalScientificTechnologies/MLAB-3Dprinter#28 Added missing STL/PNG and commited false differences after calling make on AMF/STL/PNG files.
    [Front_EURO_12V_240W.stl, Rear_EURO_12V_240W.stl, cable-holder-Nema17.stl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]
2020-05-10 UniversalScientificTechnologies/MLAB-3Dprinter#28 Removed unused M6-case-*.stl, wade-gears_small.stl and moved calibration.stl to hw/cad folder.
    [M6-case-corner.stl, M6-case-dual.stl, M6-case-simple.stl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]
2020-05-10 UniversalScientificTechnologies/MLAB-3Dprinter#28 Fixed path for STL in make clean.
2020-05-10 UniversalScientificTechnologies/MLAB-3Dprinter#28 Changed wade-gears.scad to print both gears and added set_slicing_config parameter.
    [wade-gears.scad]
2020-05-11 UniversalScientificTechnologies/MLAB-3Dprinter#28 Added version print of openscad.
2020-05-13 UniversalScientificTechnologies/MLAB-3Dprinter#28 Removed --no-gui in slic3r call in Makefile (current version doesnt have this parameter).
2020-05-13 Automatic commit from workflow
    [Front_EURO_12V_240W.amf, RAMPS_mini.amf, Rear_EURO_12V_240W.amf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]
2020-05-14 UniversalScientificTechnologies/MLAB-3Dprinter#28 Moved Revelix_render.png to doc folder. Otherwise it would be deleted by make clean (and we do not have assembly to render it again).
2020-05-14 Changes used for drawing the whole printer in OpenSCAD
    Two new .scad files were added - library for the printer and MLAB-3Dprinter itself. Parts of the printer were slightly changed for the use in the library.
    [MLAB-3Dprinter-lib.scad, Printer1.scad, y-motor.scad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]
2020-05-15 UniversalScientificTechnologies/MLAB-3Dprinter#28 Sorted AMF files and touched all files to synchronize make.
    [Front_EURO_12V_240W.amf, Front_EURO_12V_240W.stl, RAMPS_mini.amf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]
2020-05-15 UniversalScientificTechnologies/MLAB-3Dprinter#28 Sorted AMF and rebuilded everything.
    [Front_EURO_12V_240W.amf, Front_EURO_12V_240W.stl, RAMPS_mini.amf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]
2020-05-18 FIX: #25
    MLAB logo resized and moved.
    [Rear_EURO_12V_240W.scad]
2021-11-01 Add a link to magnetic heatbed design.

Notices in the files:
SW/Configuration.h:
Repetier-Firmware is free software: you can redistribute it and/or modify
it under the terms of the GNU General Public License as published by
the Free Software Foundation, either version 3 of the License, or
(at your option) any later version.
